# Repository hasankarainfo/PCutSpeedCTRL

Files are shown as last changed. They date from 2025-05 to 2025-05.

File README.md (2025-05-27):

# PCutSpeedCTRL Constant Speed Controller

<ul align="left">
    <li>It provides constant speed operation and remote control of single phase AC motor suitable for operation with 220 vac 50hz.</li>
    <li>When produced with BTA41 triac switching element, it provides usage up to 40 Ampere. In my initial tests I used a 1.2kW AC motor.</li>
    <li>The first version component cost was calculated as $3,075.</li>
    <li>Suitable for use with standard hand milling motors that are easily available on the world market.</li>
    <li>The mentioned milling motors are suitable for use in CNC machines.</li>
    <li>Any CNC controller can be connected directly and in isolation with a standard PWM output.</li>
    <li>This resource contains design and production files for hardware and firmware.</li>
    <li>PC Software used in the development process; KICAD 9 for Hardware, MOUNRIVER 2.1 IDE and C programming language were used for Firmware. OCTAVE was used to create look up tables for some mathematical equations.</li>
    <li> <a href="https://youtu.be/PU_BxYYPQiw ">Test Video Youtube Link</a>  </li>  
</ul>  

<table align="center" width=90%>
<tr>       
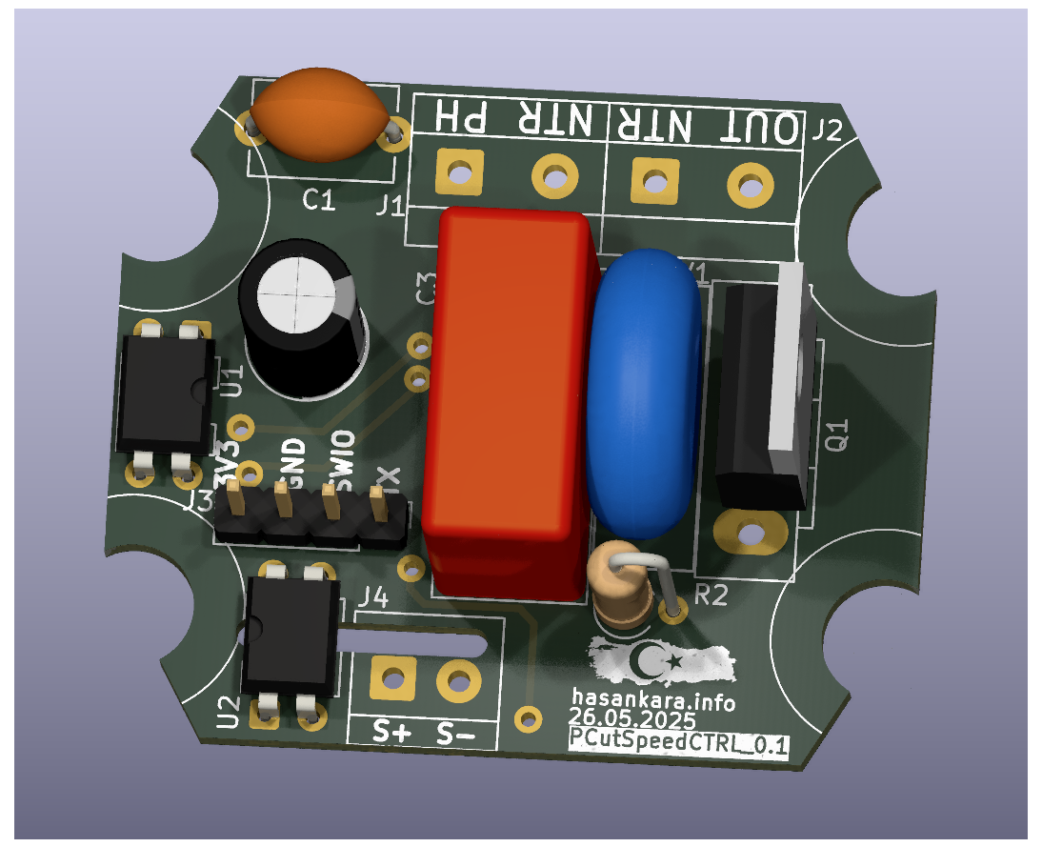
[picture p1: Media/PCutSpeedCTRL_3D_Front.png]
<td align="center"></td>
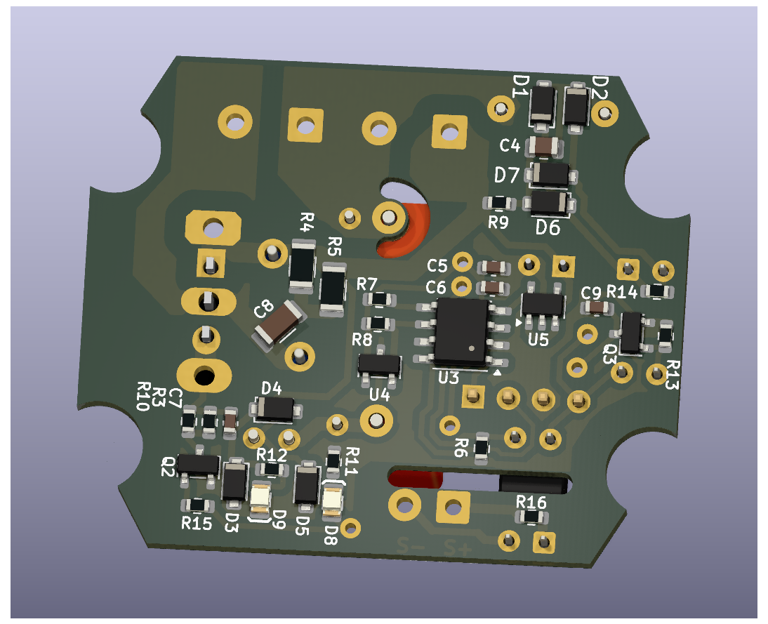
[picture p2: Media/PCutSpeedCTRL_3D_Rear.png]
<td align="center"></td>  
</tr>

<tr>  
<td align="center"> <b>3D Front</b></td>
<td align="center"> <b>3D Rear</b></td>
</tr>
</table>

## HARDWARE Detail:

### Schematic Detail:
<table align="center" width=90%>
    <tr>       
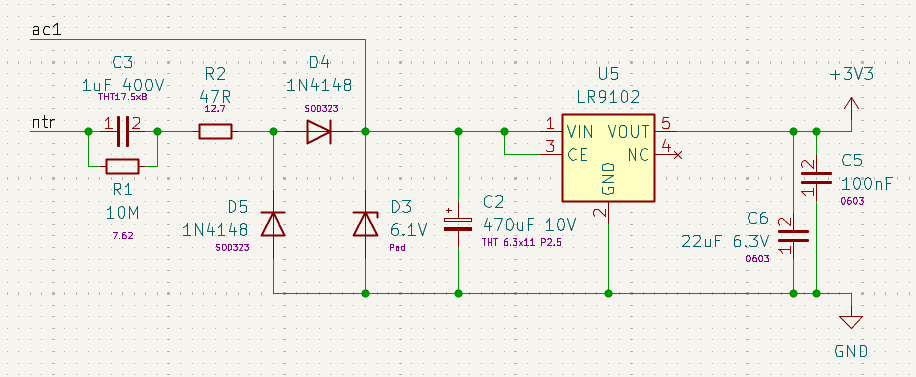
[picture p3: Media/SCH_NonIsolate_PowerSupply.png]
        <td style="width:70%"></td>
        <td>
        Non Isolated Power Supply:
            <ul><i> 
                <li> A cost-effective, non-isolated design was implemented for low voltage supply needs.  </li> 
                <li> This scheme can meet the required 30mA power requirement. This power is mainly used for MCU operation, hall effect sensor operation and TRIAC triggering.</li> 
            </i></ul>
        </td>  
    </tr>
</table>

<table align="center" width=90%>
    <tr>       
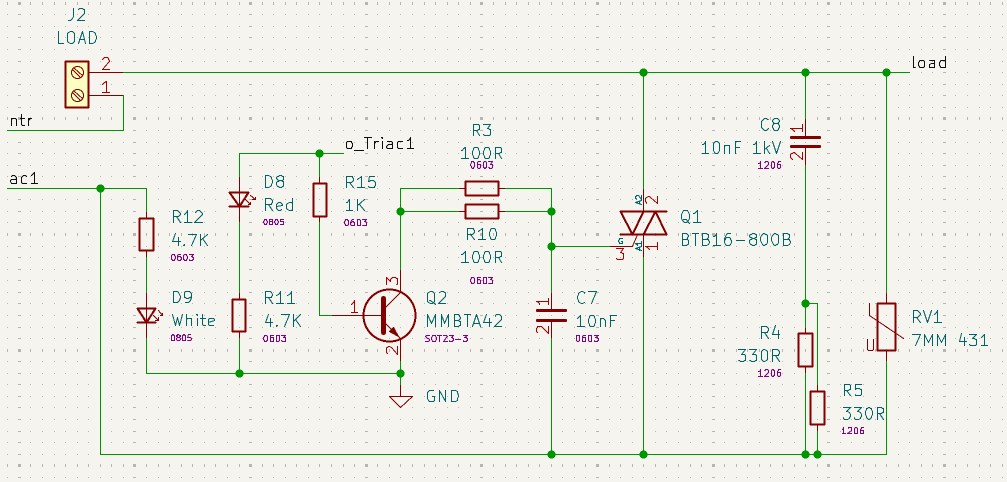
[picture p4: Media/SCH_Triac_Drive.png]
        <td style="width:70%"></td>
        <td> 
        Triac gate drive circuit:
            <ul><i>
            <li>Phase cut topology used.</li> 
            <li> Some snubber components applied.</li> 
            </i></ul>
        </td>  
    </tr>
</table>
<table align="center" width=90%>
    <tr>       
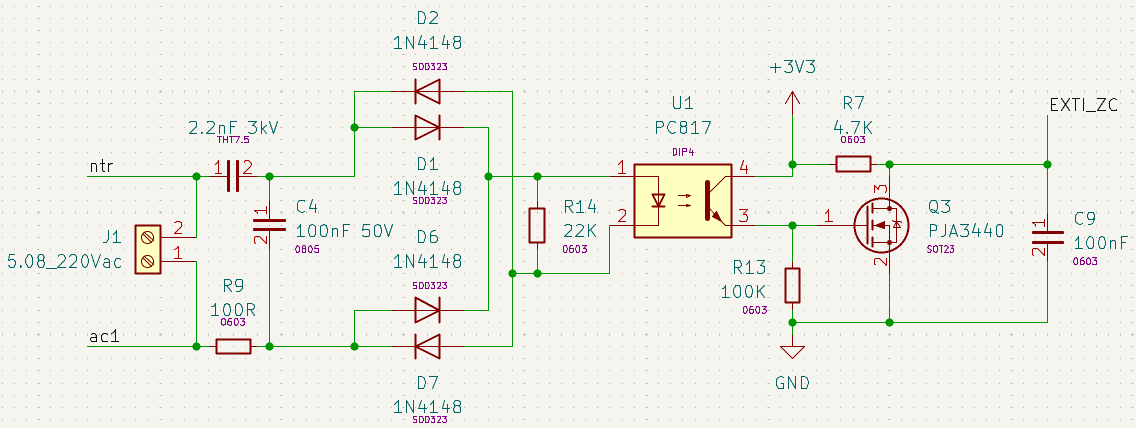
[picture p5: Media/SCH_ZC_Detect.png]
        <td style="width:70%"></td>
        <td> 
        Zero cross detection circuit:
            <ul><i>
            <li>With q3 mosfet, a faster falling edge signal is generated.
            </li> 
            </i></ul>
        </td>  
    </tr>
</table>

<table align="center" width=90%>
    <tr>       
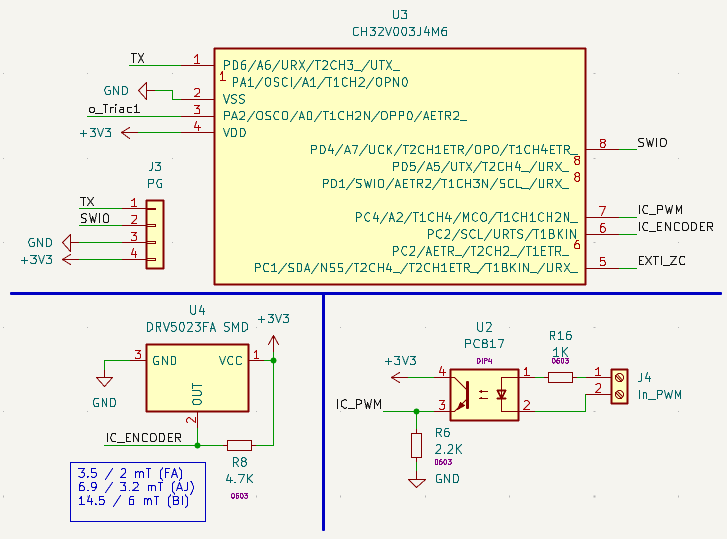
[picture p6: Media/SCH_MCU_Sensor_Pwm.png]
        <td style="width:70%"></td>
        <td> 
        MCU, Hall Sensor and PWM Input Circuit:
            <ul><i>
            <li>It was developed using the ch32v003j4m6 microcontroller from wch company.</li>
            <li> DRV5023 hall sensor was used for spindle speed measurement.</li> 
            </i></ul>
        </td>  
    </tr>
</table>

### Panelize Detail:
<ul align="left">
    <li>We use the Kikit plugin for PCB paneling.</li>
    <li>We can panelize the PCB design by running the panelize_multiple.py file located in the "/HW/Panelize/" file path.</li>
    <li>Phase cut topology used.</li>
    <li>In panelized form, a new kicad project is created automatically.</li>
</ul>  

<table align="center" width=90%>
<tr>       
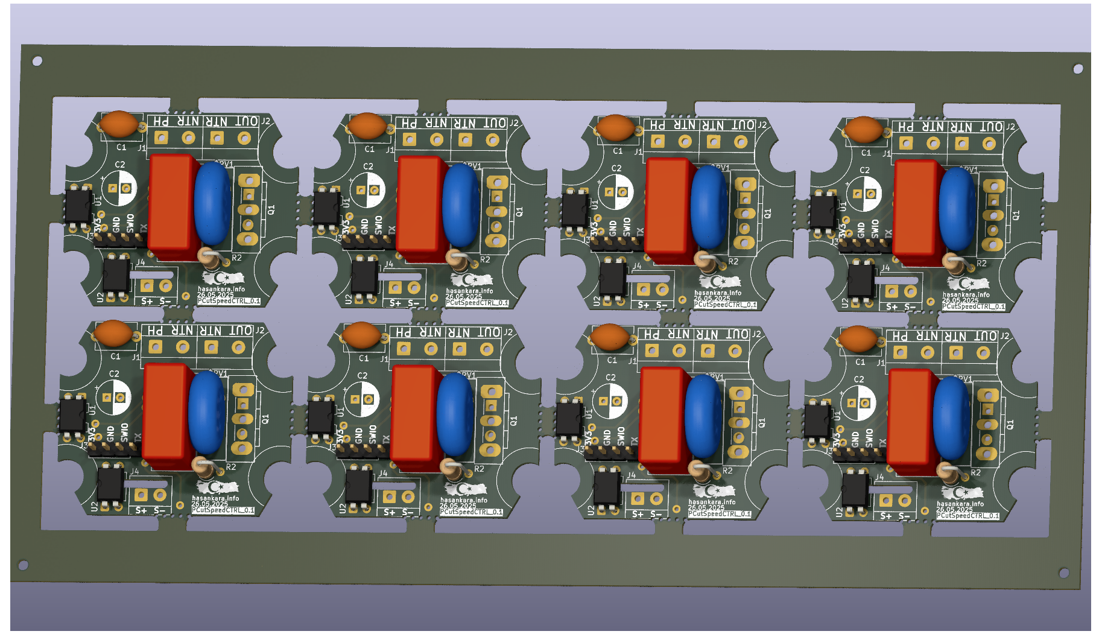
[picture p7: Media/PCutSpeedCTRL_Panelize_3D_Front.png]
<td  style="width:65%"></td>
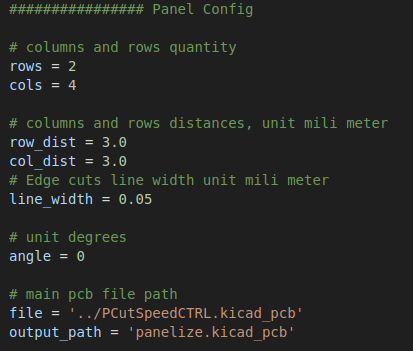
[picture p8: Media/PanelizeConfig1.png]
<td></td>  
</tr>

<tr>  
<td align="center"> <b> Panelize Wiew </b> </td>
<td align="center"> <b> Some Panel Settings in panelize_multiple.py </b></td>
</tr>
</table>

## Mechanic Detail:
<ul align="left"> 
    <li> When the AC motor top cover is opened, 4 screw holes can be seen. 
    </li>
    <li> When the top cover of the spindle motor is first opened, there will be no hole in the middle 
    </li>
    <li> A metric 5 diameter hole should be drilled along the shaft, coinciding with the center.
    </li>
    <li> While designing the PCB, compatibility was ensured by using the Mac Allister manufacturer MSR1200 model AC motor. 
    </li>
</ul>

<table align="center" width=90% >
    <tr>       
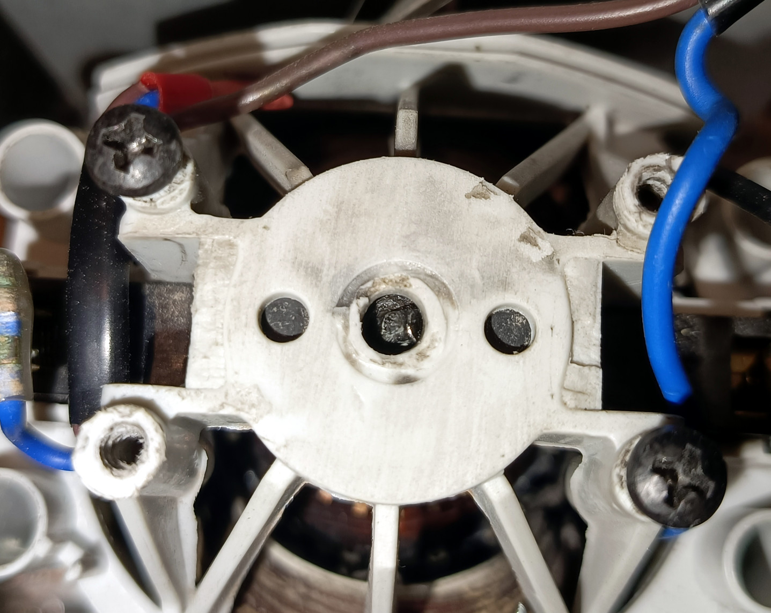
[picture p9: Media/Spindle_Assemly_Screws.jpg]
        <td style="width:70%"></td>
        <td> 
            <ul>
                <li>
                    A 3x3 mm cylindrical neodymium magnet is inserted through this hole and coupled with the shaft.
                </li>
                <li>There should be an angle of approximately ~45° between the magnet cylinder center axis and the shaft axis. 
                </li>
                <li>The shaft and magnet can be attached using super glue.
                </li>
            </ul>
        </td>  
    </tr>
</table>

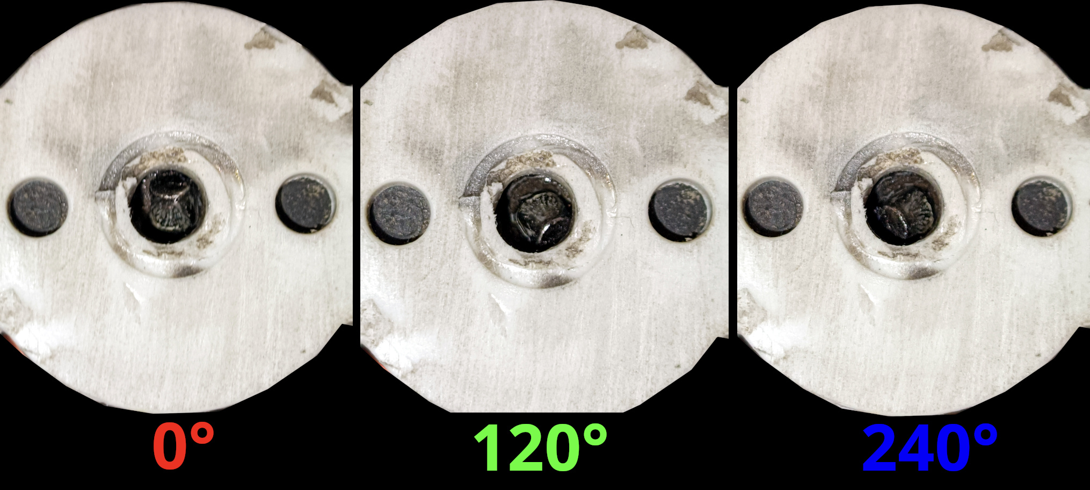
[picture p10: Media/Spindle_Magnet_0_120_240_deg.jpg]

<p align="center"> <b> When the rotor is turned to different angles, it should be confirmed that the magnet rotates together. </b> </p>

<table align="center" width=90% >
    <tr>
        <td>  
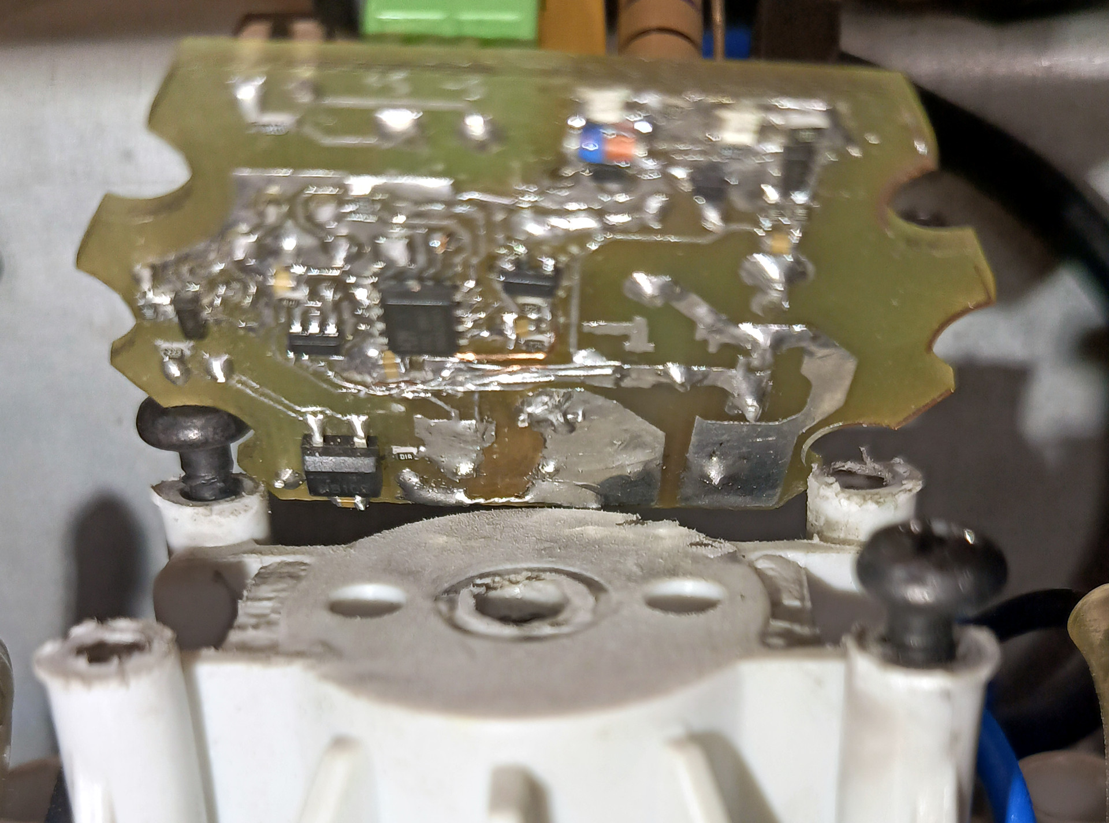
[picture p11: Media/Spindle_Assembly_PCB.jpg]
            
            <p align="center"> <b> Spindle Motor Controller assembly demonstration </b> </p>
        </td>
        <td> 
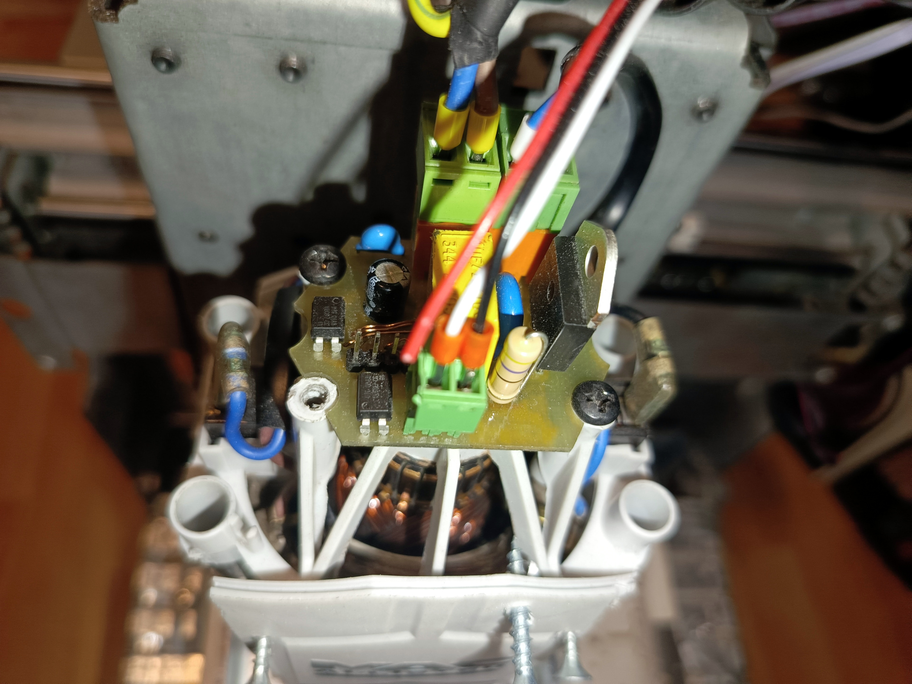
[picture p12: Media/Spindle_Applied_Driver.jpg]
            
            <p align="center"> <b> Spindle Motor Controller Driver Applied </b> </p>
        </td>
    </tr>
</table>

## Firmware Detail:

<ul align="left">
    <li>MOUNRIVER 2.1 IDE and C programming language were used for Firmware.</li>
    <li>The HYB cooperative operating system was used for the MCU resource management organization. </li>
    <li>Since the cooperative real-time operating system we use is very lightweight, it can easily adapt to the Microcontroller despite its weak memory.
    </li>
    <li> With this project, I am also sharing the cooperative operating system that I have been developing over the years as open source.</li>
    <li> I also added some libraries to the firmware that are not actively in use but could enable developments that fit the structure of the project.
    </li>
    <li>NTC temperature sensor data interpretation, ADC reading, moving average filter, some of them. 
    </li>
</ul>  

### About the main routine:
<ul align="left">
    <li>Using 2 different input capture modules, PWM input data was taken with IC1 and the magnetic sensor digital output frequency value was measured with IC2.</li>
    <li>Speed change commands have been smoothed to create a ramp between the PWM data and the target speed information.</li>
    <li>Zero Cross detection was performed using the external interrupt module. Triac triggering and PID routines were run with each ZC detection.</li>
    <li>For linearization of the system, the source signal is assumed to be a sinusoidal signal. The equation used is the integral of the half sine signal.</li>
    <li>For system linearization, PID output information was applied to the linearization function using the look up table interpolation created with the Octave PC application.</li>
    <li>Thus, a more stable closed-loop system was obtained with fixed PID coefficients.
    </li>
    <li>Duty data was evaluated as time data to convert it into TRIAC switch signal.</li>
    <li>In addition to the look up table, a firmware setting option has been added to enable linearization by measurement method.
    </li>
    <li>The firmware can be made to work with different features with a set of predefined settings.</li>
    <li>The mentioned settings can be seen in the image below, as well as in the main.c file.</li>
</ul>  

<td >  
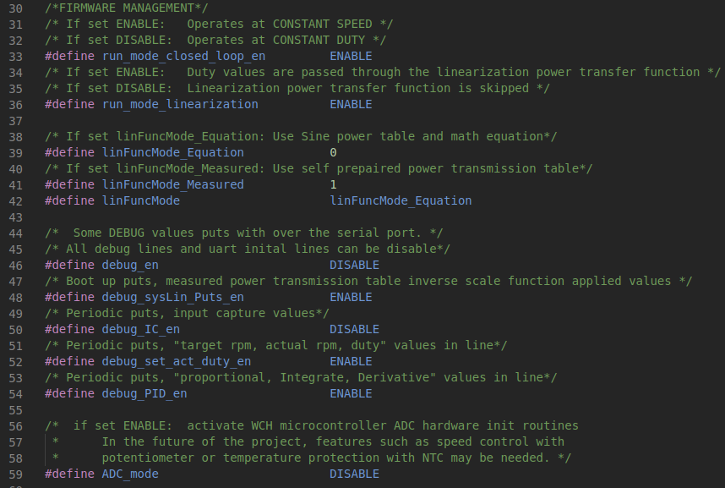
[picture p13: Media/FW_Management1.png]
    
    <p align="center"> <b> Firmware Managment Settings 1 </b> </p>
</td>

<td> 
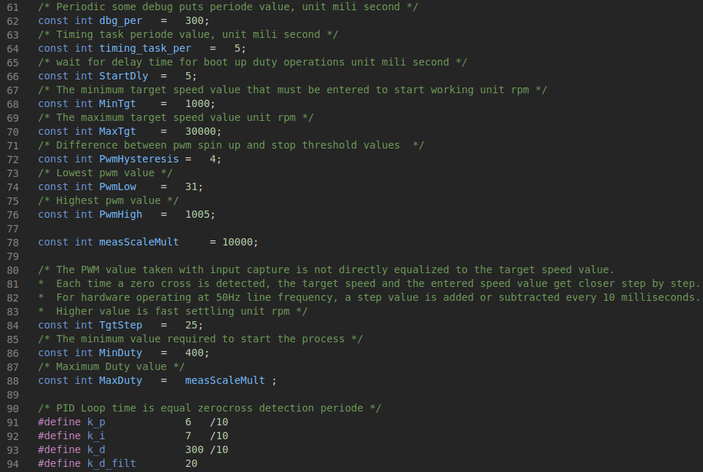
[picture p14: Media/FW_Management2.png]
    
    <p align="center"> <b> Firmware Managment Settings 2 </b> </p>
</td>

### Octave Equations Plot and Print :
<ul align="left">
    <li>The linearization table created with Octave PC software can be examined graphically and can be evaluated by copying and pasting directly into the C code.</li>
    <li>Similarly, the linearization table output from the MCU serial port output at boot up time can be directly copied and pasted into the Octave software and visually inspected. </li>
</ul>  

<table align="center" width=90% >
    <tr>
        <td>  
            
            <p align="center"> <b> Inverse Sine Power Equation Created</b> </p>
        </td>
        <td> 
            
            <p align="center"> <b> Inverse Sine Power from MCU, Equation and Measured </b> </p>
        </td>
    </tr>
</table>

## Some Tests:

<ul align="left">
    <li>As can be watched in the video link shared above, we performed some aluminum sheet and PCB drilling tests.</li>
    <li>When we apply sudden strain and sudden release tests, overshooting values of up to 800 rpm occur.</li>
    <li>The spindle motor we tested has a 30k rpm feature at full power.</li>
    <li>As is known, keeping a constant speed at low rotational speeds can be a very challenging goal.</li>
    <li>Its ability to remain at low overshoot values while at 1k rmp target speed is at a satisfactory level.
    </li>
    <li>We could observe that it does not work so stably unless linearization is applied.</li>
    <li>We made it possible to observe the result by disabling a single predefined setting via the firmware.</li>
</ul>  

<td >  
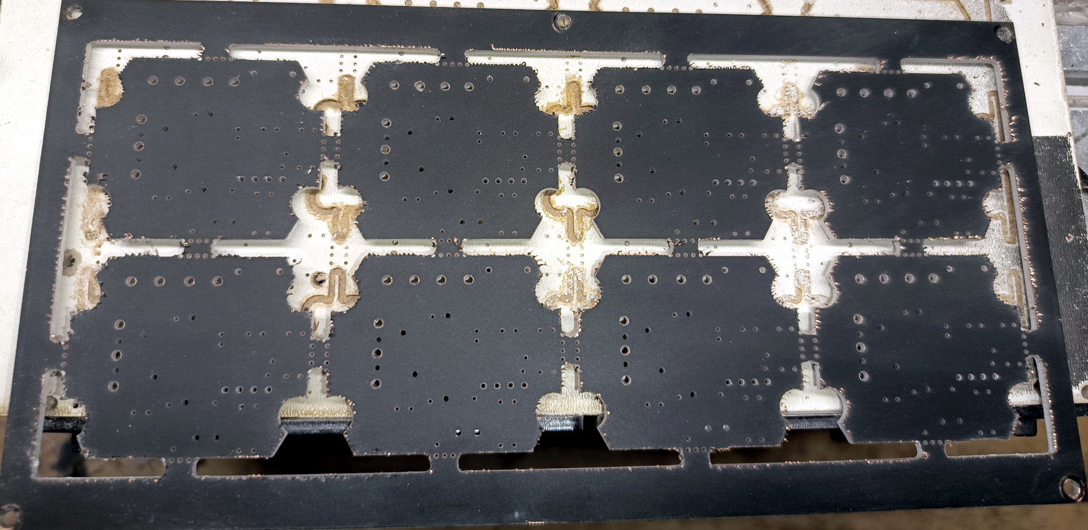
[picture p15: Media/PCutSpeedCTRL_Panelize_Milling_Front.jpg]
    
    <p align="center"> <b> PCB Milling and Edge Cut Test Front </b> </p>
</td>

<td> 
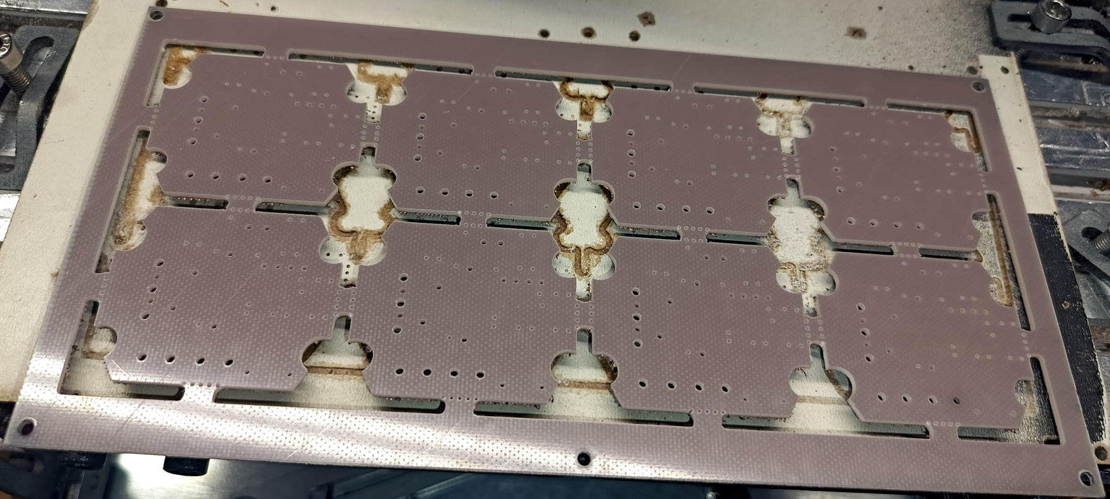
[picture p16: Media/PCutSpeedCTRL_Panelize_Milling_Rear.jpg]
    
    <p align="center"> <b> PCB Milling and Edge Cut Test Rear </b> </p>
</td>

## Production:
<ul align="left">
    <li> Gcode files created for PCB production with DIY techniques can be found in the HW/Panelize/Plot_diy folder.
    </li>
    <li>The bom list, along with supply links and unit prices, can be viewed in the "HW/bom" file path.</li>
    <li>For PCB fabrication files, files in the "HW/Plot" or "HW/Panelize/Plot" file path can be compressed and shared directly with the PCB manufacturer.</li>
</ul>

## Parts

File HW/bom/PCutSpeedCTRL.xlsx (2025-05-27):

 | Sourced | Placed | References | Value | Pad | Part Link | Part Number | Quantity | Price | Q.Price | Total
1 |  |  | C5, C9 | 100nF | 603 | https://ozdisan.com/Product/Detail/476015/CC0603KRX7R9BB104 | CC0603KRX7R9BB104 | 2 | 0.006 | 0.012 | 3.0735
2 |  |  | C1 | 2.2nF 3kV | THT7.5 | https://ozdisan.com/Product/Detail/994897/CK45-B3FD222KYNNA | CK45-B3FD222KYNNA | 1 | 0.35 | 0.35
3 |  |  | C2 | 470uF 10V | THT 6.3x11 P2.5 | https://ozdisan.com/Product/Detail/1046555/PKLH-010V471ME110-T2-5 | PKLH-010V471ME110-T2.5 | 1 | 0.05 | 0.05
4 |  |  | C3 | 1uF 400V | THT17.5x8 | https://www.motorobit.com/1uf-400vdc-15mm-damla-tipi-polyester-kondansator | KOM.KND.03.000133 | 1 | 0.1 | 0.1
5 |  |  | C4 | 100nF 50V | 805 | https://ozdisan.com/Product/Detail/497698/CC0805KRX7R9BB104 | CC0805KRX7R9BB104 | 1 | 0.006 | 0.006
6 |  |  | C6 | 22uF 6.3V | 603 | https://ozdisan.com/Product/Detail/431703/CL10A226MQ8NRNC | CL10A226MQ8NRNC | 1 | 0.038 | 0.038
7 |  |  | C7 | 10nF | 603 | https://ozdisan.com/Product/Detail/9649/CL10B103KB8NNNC | CL10B103KB8NNNC | 1 | 0.006 | 0.006
8 |  |  | C8 | 10nF 1kV | 1206 | https://ozdisan.com/Product/Detail/457676/CC1206KKX7RCBB103 | CC1206KKX7RCBB103 | 1 | 0.05 | 0.05
9 |  |  | R7, R8, R11, R12 | 4.7K | 603 | https://ozdisan.com/Product/Detail/494590/RC0603FR-074K7L | RC0603FR-074K7L | 4 | 0.0018 | 0.0072
10 |  |  | R3, R9, R10 | 100R | 603 | https://ozdisan.com/Product/Detail/341784/0603SAF1000T5E | 0603SAF1000T5E | 3 | 0.0015 | 0.0045
11 |  |  | R4, R5 | 330R | 1206 | https://ozdisan.com/Product/Detail/30259/1206S4F3300T5E | 1206S4F3300T5E | 2 | 0.0039 | 0.0078
12 |  |  | R15, R16 | 1K | 603 | https://ozdisan.com/Product/Detail/341789/0603SAF1001T5E | 0603SAF1001T5E | 2 | 0.0015 | 0.003
13 |  |  | R1 | 10M | 7.62 | Part Link | Part Number | 1 | 0.001 | 0.001
14 |  |  | R2 | 47R | 12.7 | Part Link | Part Number | 1 | 0.001 | 0.001
15 |  |  | R6 | 2.2K | 603 | https://ozdisan.com/Product/Detail/513363/RC0603FR-072K2L | RC0603FR-072K2L | 1 | 0.002 | 0.002
16 |  |  | R13 | 100K | 603 | https://ozdisan.com/Product/Detail/339374/0603SAF1003T5E | 0603SAF1003T5E | 1 | 0.0015 | 0.0015
17 |  |  | R14 | 22K | 603 | https://ozdisan.com/Product/Detail/341794/0603SAF2202T5E | 0603SAF2202T5E | 1 | 0.0015 | 0.0015
18 |  |  | D1, D2, D4, D5, D6, D7 | 1N4148 | SOD323 | https://ozdisan.com/Product/Detail/453557/1N4148WS-HT | 1N4148WS-HT | 6 | 0.014 | 0.084
19 |  |  | D3 | 6.1V | Pad | https://ozdisan.com/Product/Detail/14547/ZMD6-2 | ZMD6.2 | 1 | 0.05 | 0.05
20 |  |  | D8 | Red | 805 | https://ozdisan.com/Product/Detail/490003/HL-PSC-2012H233W-HF4 | HL-PSC-2012H233W-HF4 | 1 | 0.024 | 0.024
21 |  |  | D9 | White | 805 | https://ozdisan.com/Product/Detail/490003/HL-PSC-2012H233W-HF4 | HL-PSC-2012H233W-HF4 | 1 | 0.024 | 0.024
22 |  |  | U1, U2 | PC817 | DIP4 | https://ozdisan.com/Product/Detail/502879/UPC817CG-D04-T | UPC817CG-D04-T | 2 | 0.08 | 0.16
23 |  |  | U3 | CH32V003J4M6 |  | https://aliexpress.com/item/1005005263084570.html | CH32V003J4M6 | 1 | 0.35 | 0.35
24 |  |  | U4 | DRV5023FA SMD |  | https://www.digikey.com/en/products/detail/texas-instruments/DRV5023AJQDBZRQ1/5056028 | 296-49623-1-ND | 1 | 0.8 | 0.8
25 |  |  | U5 | LR9102 |  | https://ozdisan.com/Product/Detail/700883/LR9102G-33-AF5-R | LR9102G-33-AF5-R | 1 | 0.09 | 0.09
26 |  |  | Q1 | BTB16-800B |  | https://www.direnc.net/btb16-800-triac-800v-16a-snubberless-triac-to-220ab |  | 1 | 0.48 | 0.48
27 |  |  | Q2 | MMBTA42 | SOT23-3 | https://ozdisan.com/Product/Detail/348651/MMBTA42R100001 | MMBTA42_R1_00001 | 1 | 0.03 | 0.03
28 |  |  | Q3 | PJA3440 | SOT23 | https://ozdisan.com/Product/Detail/517995/PJA3440R200001 | PJA3440_R2_00001 | 1 | 0.1 | 0.1
29 |  |  | RV1 | 7MM 431 |  | https://ozdisan.com/Product/Detail/339778/TVR07431KSABY | TVR07431KSABY | 1 | 0.05 | 0.05
30 |  |  | J1 | 5.08_220Vac |  | https://ozdisan.com/Product/Detail/1042573/ZB2EDGV-5-08-2P | ZB2EDGV-5.08-2P | 1 | 0.045 | 0.045
31 |  |  | J2 | LOAD |  | https://ozdisan.com/Product/Detail/1042573/ZB2EDGV-5-08-2P | ZB2EDGV-5.08-2P | 1 | 0.045 | 0.045
32 |  |  | J4 | In_PWM |  | https://ozdisan.com/Product/Detail/707708/15EDGVC-3-5-02P-12-00AH | 15EDGVC-3.5-02P-12-00AH | 1 | 0.1 | 0.1

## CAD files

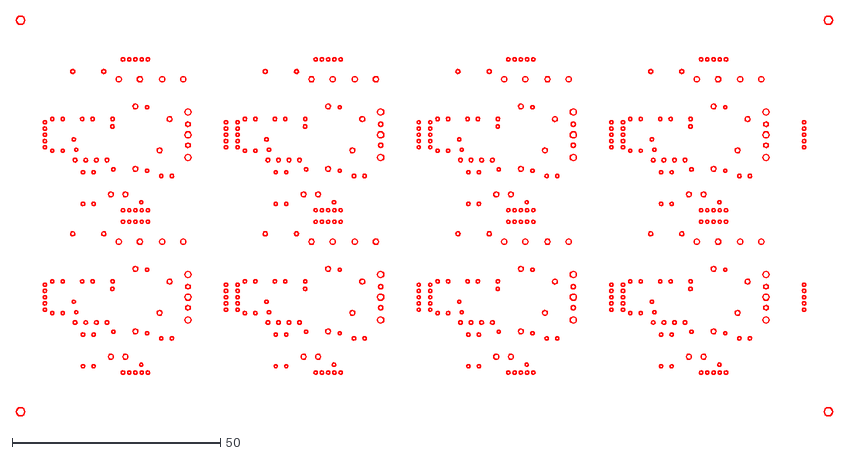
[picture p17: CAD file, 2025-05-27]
HW/Panelize/Plot_diy/panelize.dxf
196.0 x 96.0

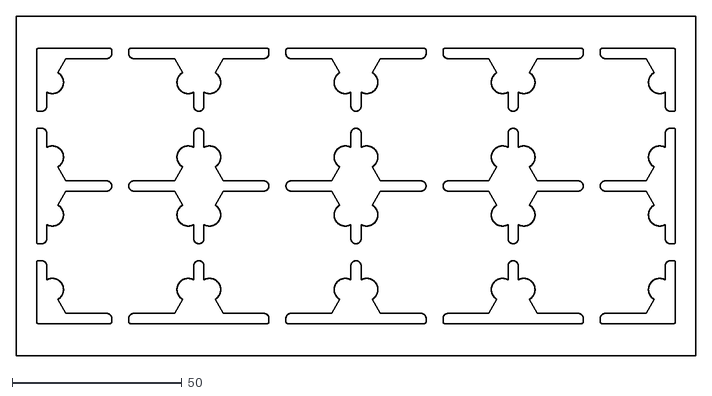
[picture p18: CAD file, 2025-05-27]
HW/Panelize/Plot_diy/panelize-Edge_Cuts.dxf
200.0 x 100.0

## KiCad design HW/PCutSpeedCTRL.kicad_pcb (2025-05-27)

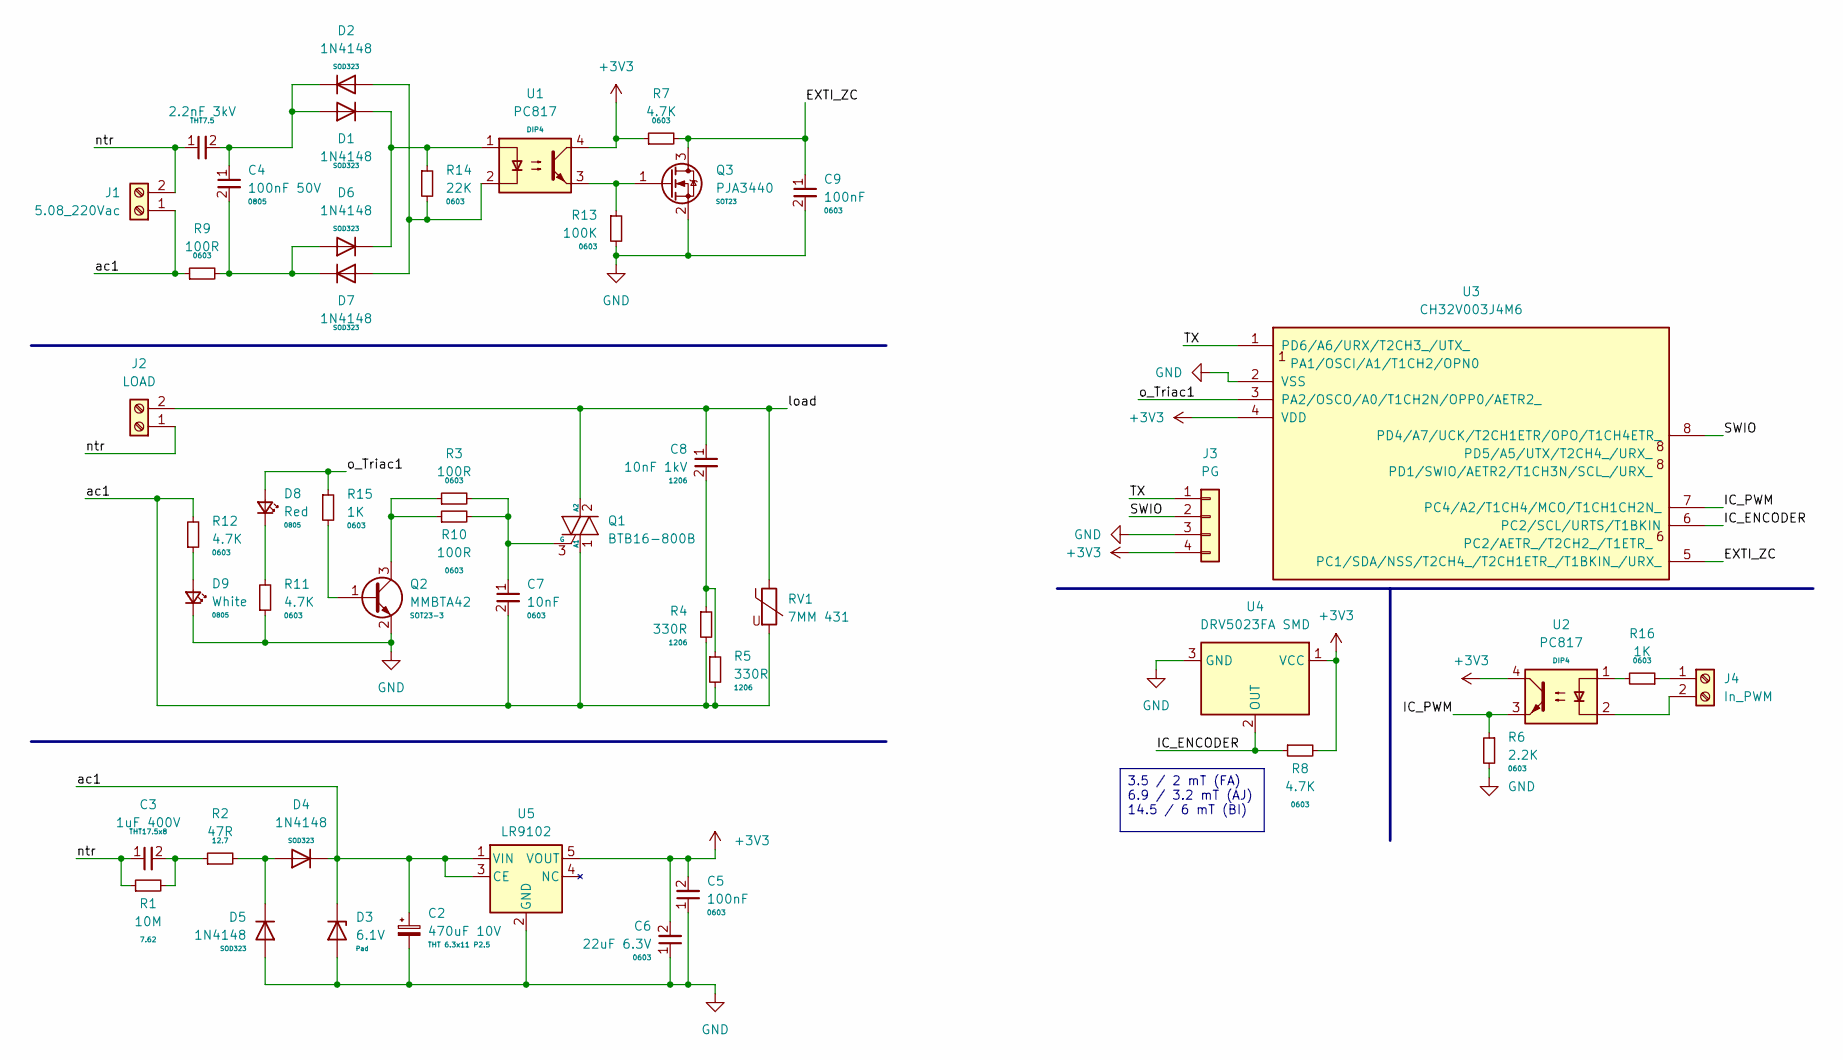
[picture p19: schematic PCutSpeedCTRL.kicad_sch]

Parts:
C1: 2.2nF 3kV; C_Disc_D7.5mm_W5.0mm_P7.50mm; Part Number CK45-B3FD222KYNNA
C2: 470uF 10V; CP_Radial_D6.3mm_H11.0mm_P2.50mm; Part Number PKLH-010V471ME110-T2.5
C3: 1uF 400V; C_Rect_L18.0mm_W8.0mm_P15.00mm_FKS3_FKP3; Part Number KOM.KND.03.000133
C4: 100nF 50V; C_0805_2012Metric_SmallPad; Part Number CC0805KRX7R9BB104
C5, C9: 100nF; C_0603_1608Metric_SlimPad; Part Number CC0603KRX7R9BB104
C6: 22uF 6.3V; C_0603_1608Metric; Part Number CL10A226MQ8NRNC
C7: 10nF; C_0603_1608Metric_SlimPad; Part Number CL10B103KB8NNNC
C8: 10nF 1kV; C_1206_3216Metric_SlimPad; Part Number CC1206KKX7RCBB103
D1, D2, D4, D5, D6, D7: 1N4148; D_SOD-123F-s; Part Number 1N4148WS-HT
D3: 6.1V; D_SOD-123F-s; Part Number ZMD6.2
D8: Red; LED_0805_2012Metric-s; Part Number HL-PSC-2012H233W-HF4
D9: White; LED_0805_2012Metric-s; Part Number HL-PSC-2012H233W-HF4
J1: 5.08_220Vac; TerminalBlock_MetzConnect_Type101_RT01602HBWC_1x02_P5.08mm_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; Part Number ZB2EDGV-5.08-2P
J2: LOAD; TerminalBlock_MetzConnect_Type101_RT01602HBWC_1x02_P5.08mm_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; Part Number ZB2EDGV-5.08-2P
J3: PG; PinHeader_1x04_P2.54mm_Vertical
J4: In_PWM; TerminalBlock_4Ucon_1x02_P3.50mm_Horizontal; Part Number 15EDGVC-3.5-02P-12-00AH
Q1: BTB16-800B; TO-220-3_Vertical_HV_TO247_Applied
Q2: MMBTA42; SOT-23-3-s; Part Number MMBTA42_R1_00001
Q3: PJA3440; SOT-23-3-s; Part Number PJA3440_R2_00001
R1: 10M; R_Axial_DIN0207_L6.3mm_D2.5mm_P15.24mm_Horizontal; Part Link Part Link
R2: 47R; R_Axial_DIN0309_L9.0mm_D3.2mm_P2.54mm_Vertical; Part Link Part Link
R3, R9, R10: 100R; R_0603_1608Metric; Part Number 0603SAF1000T5E
R4, R5: 330R; R_1206_3216Metric_SlimPad; Part Number 1206S4F3300T5E
R6: 2.2K; R_0603_1608Metric; Part Number RC0603FR-072K2L
R7, R8, R11, R12: 4.7K; R_0603_1608Metric; Part Number RC0603FR-074K7L
R13: 100K; R_0603_1608Metric; Part Number 0603SAF1003T5E
R14: 22K; R_0603_1608Metric; Part Number 0603SAF2202T5E
R15, R16: 1K; R_0603_1608Metric; Part Number 0603SAF1001T5E
RV1: 7MM 431; RV_Disc_D15.5mm_W5.4mm_P7.5mm_Spec; Part Number TVR07431KSABY
U1, U2: PC817; DIP-4_W7.62mm; Part Number UPC817CG-D04-T
U3: CH32V003J4M6; SO-8_3.9x4.9mm_P1.27mm; Part Number CH32V003J4M6
U4: DRV5023FA SMD; SOT-23-3-s; Part Number 296-49623-1-ND
U5: LR9102; TSOT-23-5_SlimPad; Part Number LR9102G-33-AF5-R

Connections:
+3V3: C5.2, C6.2, J3.4, R7.1, R8.2, U1.4, U2.4, U3.4 (VDD), U4.1 (VCC), U5.5 (VOUT)
/EXTI_ZC: C9.1, Q3.3 (D), R7.2, U3.5 (PC1/SDA/NSS/T2CH4_/T2CH1ETR_/T1BKIN_/UR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)
/IC_ENCODER: R8.1, U3.6 (PC2/SCL/URTS/T1BKIN), U4.2 (OUT)
/IC_PWM: R6.1, U2.3, U3.7 (PC4/A2/T1CH4/MCO/T1CH1CH2N_)
/SWIO: J3.2, U3.8 (PD4/A7/UCK/T2CH1ETR/OPO/T1CH4ETR_)
/TX: J3.1, U3.1 (PD6/A6/URX/T2CH3_/UTX_)
/ac1: C2.1, C7.2, D3.1 (K), D4.1 (K), J1.1, Q1.1 (A1), R4.2, R5.2, R9.1, R12.2, RV1.2, U5.1 (VIN), U5.3 (CE)
/load: C8.1, J2.2, Q1.2 (A2), RV1.1
/ntr: C1.1, C3.1, J1.2, J2.1, R1.1
/o_Triac1: D8.2 (A), R15.1, U3.3 (PA2/OSCO/A0/T1CH2N/OPP0/AETR2_)
GND: C2.2, C5.1, C6.1, C9.2, D3.2 (A), D5.2 (A), D9.1 (K), J3.3, Q2.2 (E), Q3.2 (S), R6.2, R11.1, R13.2, U3.2 (VSS), U4.3 (GND), U5.2 (GND)
unnamed: C3.2, R1.2, R2.1
unnamed: C8.2, R4.1, R5.1
unnamed: C1.2, C4.1, D1.2 (A), D2.1 (K)
unnamed: D1.1 (K), D6.1 (K), R14.1, U1.1
unnamed: D2.2 (A), D7.2 (A), R14.2, U1.2
unnamed: D4.2 (A), D5.1 (K), R2.2
unnamed: C4.2, D6.2 (A), D7.1 (K), R9.2
unnamed: D8.1 (K), R11.2
unnamed: D9.2 (A), R12.1
unnamed: J4.1, R16.1
unnamed: J4.2, U2.2
unnamed: C7.1, Q1.3 (G), R3.2, R10.2
unnamed: Q2.1 (B), R15.2
unnamed: Q2.3 (C), R3.1, R10.1
unnamed: Q3.1 (G), R13.1, U1.3
unnamed: R16.2, U2.1

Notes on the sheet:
3.5 / 2 mT (FA) 6.9 / 3.2 mT (AJ) 14.5 / 6 mT (BI)

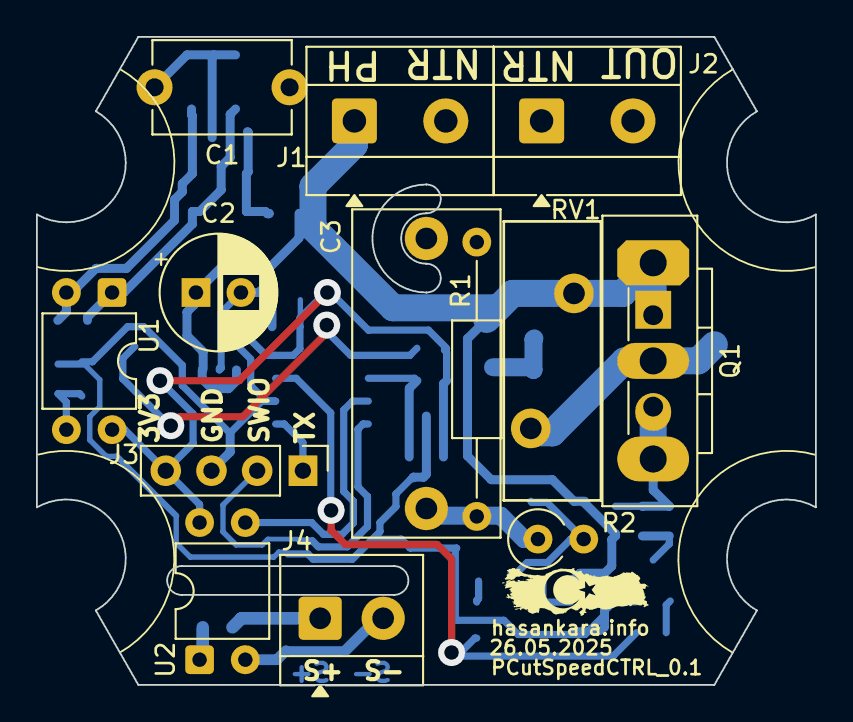
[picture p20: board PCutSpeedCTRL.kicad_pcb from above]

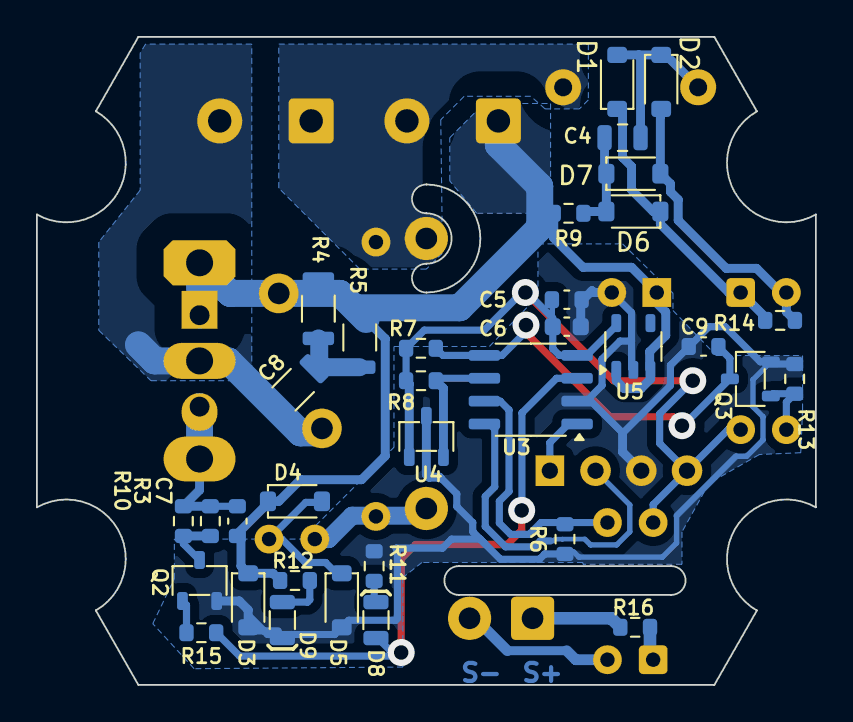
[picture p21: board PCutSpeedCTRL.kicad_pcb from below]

Board: 2 copper layers, 43.3 x 36.0 mm, 47 parts (34 on the bottom side), 27 nets.

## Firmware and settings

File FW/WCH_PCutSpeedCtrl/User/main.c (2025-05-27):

/********************************** (C) COPYRIGHT *******************************
 * File Name          : main.c
 * Author             : hasankarainfo
 * Version            : V_01b
 * Date               : 2025/04/15
 * Description        : WCH_PCutSpeedCTRL main program body. 
 *	It ensures that the motor, suitable for operation with 220 vac 50hz, operates at constant speed.
 *	It was developed using the ch32v003j4m6 microcontroller from wch company.
 *	Some benefits of the firmware;
 *	Suitable for use with standard hand milling motors that are easily available on the world market.
 *	The mentioned milling motors are suitable for use in CNC machines,
 *	Any CNC controller can be connected directly and in isolation with a standard PWM output.
 *********************************************************************************
 * Copyright (c) hasankarainfo
 *******************************************************************************/

#include "init_wch.h"
#include "debug.h"
#include <stdbool.h>
#include "diff_int.h"
#include "NTC_Table.h"

#include "hybos_threads.h"

///\\\-\---\----\------\-------\--------\----------\-----------\-------------
#define DISABLE		0
#define ENABLE 		!DISABLE

///\\\-\---\----\------\-------\--------\----------\-----------\-------------
/*FIRMWARE MANAGEMENT*/
/* If set ENABLE:	Operates at CONSTANT SPEED */
/* If set DISABLE:	Operates at CONSTANT DUTY */
#define run_mode_closed_loop_en			ENABLE
/* If set ENABLE:	Duty values are passed through the linearization power transfer function */
/* If set DISABLE:	Linearization power transfer function is skipped */
#define run_mode_linearization			ENABLE

/* If set linFuncMode_Equation: Use Sine power table and math equation*/
#define linFuncMode_Equation			0
/* If set linFuncMode_Measured: Use self prepaired power transmission table*/
#define linFuncMode_Measured			1
#define linFuncMode						linFuncMode_Equation

/*	Some DEBUG values puts with over the serial port. */
/* All debug lines and uart inital lines can be disable*/
#define debug_en						DISABLE
/* Boot up puts, measured power transmission table inverse scale function applied values */
#define debug_sysLin_Puts_en			ENABLE
/* Periodic puts, input capture values*/
#define debug_IC_en						DISABLE
/* Periodic puts, "target rpm, actual rpm, duty" values in line*/
#define debug_set_act_duty_en			ENABLE
/* Periodic puts, "proportional, Integrate, Derivative" values in line*/
#define debug_PID_en					ENABLE

/*	if set ENABLE:	activate WCH microcontroller ADC hardware init routines
 *		In the future of the project, features such as speed control with 
 *		potentiometer or temperature protection with NTC may be needed. */
#define ADC_mode 						DISABLE

/* Periodic some debug puts periode value, unit mili second */
const int dbg_per	=	300;
/* Timing task periode value, unit mili second */
const int timing_task_per	=	5;
/* wait for delay time for boot up duty operations unit mili second */
const int StartDly	=	5;
/* The minimum target speed value that must be entered to start working unit rpm */
const int MinTgt 	=	1000;
/* The maximum target speed value unit rpm */
const int MaxTgt 	=	30000;
/* Difference between pwm spin up and stop threshold values  */
const int PwmHysteresis =	4; 
/* Lowest pwm value */
const int PwmLow 	=	31;
/* Highest pwm value */
const int PwmHigh 	=	1005;

const int measScaleMult 	= 10000;

/* The PWM value taken with input capture is not directly equalized to the target speed value.
*  Each time a zero cross is detected, the target speed and the entered speed value get closer step by step.
*  For hardware operating at 50Hz line frequency, a step value is added or subtracted every 10 milliseconds.
*  Higher value is fast settling unit rpm */
const int TgtStep 	=	25;
/* The minimum value required to start the process */
const int MinDuty 	=	400; 
/* Maximum Duty value */
const int MaxDuty 	=	measScaleMult ;

/* PID Loop time is equal zerocross detection periode */
#define	k_p				6	/10
#define	k_i				7	/10
#define	k_d				300	/10
#define	k_d_filt		20
///\\\-\---\----\------\-------\--------\----------\-----------\-------------
/*EXTERNS*/
extern hyb_ts *hyb_cooperative_create(void);
extern hyb_ret_te hyb_cooperative_handler(hyb_ts *hyb);
///\\\-\---\----\------\-------\--------\----------\-----------\-------------
const int Periode =	10000; /* zero cross (zc) periode cycle time. unit micro second (us)*/
#define k_rpm				(60*1000)

#if (linFuncMode == linFuncMode_Equation)

/* The table is created With Octave PC Application */
const uint16_t inverseSinePowerAmplitude = 10000;
const uint16_t inverseSinePowerLength = 101;
const uint16_t inverseSinePowerTable[101] = {
   0,  638,  903, 1108, 1282, 1436, 1575, 1705, 1826, 1940,
2048, 2152, 2252, 2348, 2441, 2532, 2620, 2706, 2789, 2871,
2952, 3031, 3108, 3184, 3259, 3333, 3406, 3478, 3550, 3620,
3690, 3759, 3828, 3896, 3963, 4030, 4097, 4163, 4229, 4294,
4359, 4424, 4489, 4553, 4617, 4681, 4745, 4809, 4873, 4936,
5000, 5064, 5127, 5191, 5255, 5319, 5383, 5447, 5511, 5576,
5641, 5706, 5771, 5837, 5903, 5970, 6037, 6104, 6172, 6241,
6310, 6380, 6450, 6522, 6594, 6667, 6741, 6816, 6892, 6969,
7048, 7129, 7211, 7294, 7380, 7468, 7559, 7652, 7748, 7848,
7952, 8060, 8174, 8295, 8425, 8564, 8718, 8892, 9097, 9362,
10000};

#elif (linFuncMode == linFuncMode_Measured)
/*	Attention Please;
	The minimum value of all values in the table must be at index [0]
	The maximum value of all values in the table must be at index [Length-1]

	Duty is increased at equal intervals and the feedback value is recorded.
	When performing this operation, "run_mode_closed_loop_en DISABLE", must be used.
	When performing this operation, "run_mode_linearization DISABLE", must be used.
*/
/*	Duty - Power Table	 */
const uint16_t measTable[] 	= {75,121,202,321,452,555,655,716,755,762,765};
const int measTable_Length 	= (sizeof(measTable)/2);
#endif
///\\\-\---\----\------\-------\--------\----------\-----------\-------------

static long limit(long x, long min, long max) {
	long val = x;
	if (max < min) {
		if (val > min)
			val = min;
		if (val < max)
			val = max;
	} else {
		if (val > max)
			val = max;
		if (val < min)
			val = min;
	}
	return val;
}
static long map(long x, long in_min, long in_max, long out_min, long out_max) {
	long val = (x - in_min) * (out_max - out_min) / (in_max - in_min) + out_min;
	val = limit(val, out_min, out_max);

	return val;
}
///\\\-\---\----\------\-------\--------\----------\-----------\-------------
/*SOME GLOBAL VARIABLES*/

int Summ = 0;
int prevError = 0;
int Portional = 0;
int Deriv = 0;
int Duty = 0;
int error = 0;
int tgt_rpm;
int pwm_in;
int act_rpm;
int act_ms;
int calc_us;

uint8_t	f_cnt1 = 0;
uint8_t	f_cnt2 = 0;

hyb_ts	*hyb_globes, *hyb_zc_detect, *hyb_triac_sgn;
diff_ts d_zc;
///\\\-\---\----\------\-------\--------\----------\-----------\-------------
/*VARIABLES and FUNCTIONS for ADC*/
#if (ADC_mode == ENABLE)

typedef enum {
	arg_throttle,
	arg_periode,
	//arg_min, /**/
	//arg_offset,
	arg_size
} arg_enumeration;
//static uint8_t adc_chs[]={ADC_Channel_2, ADC_Channel_0 , ADC_Channel_3, ADC_Channel_1};
// static uint8_t adc_chs[]={ADC_Channel_2, ADC_Channel_0 };
static uint8_t adc_chs[]={ADC_Channel_6, ADC_Channel_7 };
static uint8_t adc_nbrs = arg_size;

static diff_ts d_adc[arg_size];
long arg[arg_size];
long adc_val[arg_size];
long per_raw;

///\\\-\---\----\------\-------\--------\----------\-----------\-------------
void ADC_Result_Rdy(void) {
	//	temp = NTC_ADC2Temperature(ntc);

	//	arg[arg_periode] = map(diff_peek(&d_adc[arg_periode]) , 25,1010,0 , 12000);
	//	arg[arg_min] = map(diff_peek(&d_adc[arg_min]) , 0,1020, 0 , arg[arg_periode]/2);
	//	arg[arg_throttle] = map(diff_peek(&d_adc[arg_throttle]), 25, 1010, 0, arg[arg_periode]- 500);
	//	arg[arg_throttle] = map(diff_peek(&d_adc[arg_throttle]), 25, 1010, 0, 100);
	//	PWM_SET(arg[arg_throttle]/5);
}
#endif
///\\\-\---\----\------\-------\--------\----------\-----------\-------------


#if (linFuncMode == linFuncMode_Equation)

///\\\-\---\----\------\-------\--------\----------\-----------\-------------
int inverseScaleEquation(int in)
{
	int step =0;
	int y1;
	int tmp = 0;
	int val = in;
	
	step = measScaleMult/2;
	y1 = step;

	while(  1 )
	{
		step/=2;
		//tmp = sinus_power_equation(y1);
		if(val < tmp)
		{
			y1-=step;
		}else if(val > tmp){
			y1+=step;
		} else{
			/* exact found*/
			break;
		}
		if(step<1)
		{
			break;
		}
		
	}
		
	return y1;
}
///\\\-\---\----\------\-------\--------\----------\-----------\-------------
int interpolateTable(int in, const uint16_t *ptr, int len, int Amp)
{
	/* Example; tmp = 250 => ind = 2, valn = 1108, val= 903,  result = 1005 */
	in &=0xefffffff;
	len &=0xefffffff;
	int ind =  in / (len-1);
	if(ind >= (len-1)  ) 
	{
		return ptr[len-1];
	}
	//								step*ind	tmp		step*(ind+1)
	/* result = val + delta_y / (	  200		250		  300)			*/
	int val = ptr[ind];
	int valn = ptr[ind+1];
	//result = val + (valn-val) * (tmp - ind*step )/ step;
	return val + (valn-val) * (in*(len-1) - ind*Amp )/ Amp;
}
#elif (linFuncMode == linFuncMode_Measured)
/*********************************************************************
 * @fn      inverseInterpolateTable
 *
 * @brief   The lookup table obtained with the unit impulse response of the system is processed.
 *			The table is scaled and inverse is applied.
 *			Two points are detected and linear interpolation is applied.
 *
 * @param 	in - entering value
 *			ptr - Table Pointer
 *			len - Table Length
 *			scale - scale factor value
 *
 * @return  Resulting value
 */
int inverseInterpolateTable(int in, const uint16_t *ptr, int len, int scale)
{
	int f_val = 0;
	int l_val = 0;
	int width = 0;
	int val=0, valn=0;
	int j=0;
	int delta_x = 0;
	int delta_y = 0;

	f_val = ptr[0];
	//f_val = 0;
	l_val = ptr[len - 1];
	width = l_val - f_val;

	while(  j < len )
	{
		val = (ptr[j] - f_val)* scale /width ;//1087
		j++;
		valn= (ptr[j] - f_val) * scale /width ;//1753

		/* search index*/
		if(val <= in && in <= valn)
		{
			break;
		}
	}

	/* example => valn = 5000, val = 1000, in = 4000, j = 5  */
	delta_y = (valn-val); // delta_y = 4000
	/* delta_x = ((j+1) -j) * scale/len;	*/
	delta_x = scale / len; // delta_x = 909

	/*
	val 	-> in 		3 step
	in 		-> valn 	1 step
	
	fraction = (delta_x)	* ( (in-val) 	/	delta_y 	)
	fraction = (delta_x) 	* (	(3 step) 	/ 	(4 step) 	)
	fraction = 	 909 		* 		3 		/ 		4 			= 682

	result = j * delta_x + fraction
	result = j * delta_x + (delta_x)* ( (in-val) 	/	delta_y 	)
	result = j * delta_x + (delta_x)* ( (in-val) 	/	(valn-val) 	)
				5	  909		 909		 3000 		/ 	  4000
	result = 5 * 909 + 682 = 5227
	*/

	if(delta_y == 0) return 0;
	//return  j * delta_x +  (in - val) * delta_x  / delta_y; 

	// for more fraction
	return  j * scale / len +  (in - val) * scale / len / delta_y; 
}
///\\\-\---\----\------\-------\--------\----------\-----------\-------------
#endif
///\\\-\---\----\------\-------\--------\----------\-----------\-------------

int sys_linearization(int numerator)
{
	/* system linearisation with the sinus function integral and power equation targeting*/
	/* "https://www.desmos.com/calculator/x6jm10zomc" link available to see the chart*/
	int tmp = numerator;
#if (linFuncMode == linFuncMode_Equation)
	// tmp = map(tmp,MinDuty,measScaleMult, MinDuty, MaxDuty);

	tmp = interpolateTable(tmp, inverseSinePowerTable, inverseSinePowerLength, inverseSinePowerAmplitude);

#elif (linFuncMode == linFuncMode_Measured)
	
	tmp = inverseInterpolateTable(tmp, measTable, measTable_Length, measScaleMult);
#endif

	return tmp;
}
///\\\-\---\----\------\-------\--------\----------\-----------\-------------

void task_zc_detect(hyb_ts *hyb){
	hyb_begin;

	while (1)
	{
		if(hyb_get_sgnparam() == 0)
			hyb_suspend();

		hyb_get_sgnparam() = 0;

		if(tgt_rpm   < MinTgt){
			Duty = 0;
			Summ = 0;
			error = tgt_rpm - act_rpm;
			prevError = error;
			continue;
		}
	
#if (run_mode_closed_loop_en == ENABLE)
		int tmp = 0;
		int k_sens_reaction = limit(act_ms,10,300);
		error = tgt_rpm - act_rpm;

		/* P */
		Portional = error  * k_p ;
		Portional = limit(Portional, -measScaleMult/2, measScaleMult/2 );

		/* I */
		tmp = error  * k_i  / k_sens_reaction;
		Summ += tmp;
		Summ = limit(Summ, 200, measScaleMult);

		/* D */
		tmp = (error - prevError) * k_d / k_sens_reaction;
		//tmp = (error - prevError) * k_d ;
		Deriv = (tmp + Deriv*k_d_filt)/(k_d_filt+1);/* filter apply*/
		Deriv = limit(Deriv, -measScaleMult/2, measScaleMult/2 );
		
		/* TOTAL */
		Duty = Portional + Summ + Deriv ;
		prevError = error;
#else 
		/* tgt_rpm values must be remap for duty*/
		if(tgt_rpm >= MinTgt)
			Duty = map(tgt_rpm, MinTgt, MaxTgt, 0, MaxDuty);
		else Duty = 0;

#endif
	Duty = limit(Duty, 0, measScaleMult );

#if (run_mode_linearization == ENABLE)
		Duty = sys_linearization(Duty);
#endif
		
		calc_us = diff_get(&d_zc);
		if(Duty >= MinDuty )
		{
			int time = Periode - Duty - calc_us;
			hyb_wait(time);
			/* If the zc signal occurs during this time, the currently running cycle is skipped.*/
			if(hyb_get_sgnparam() == 0)
			{
				hyb_notify(hyb_triac_sgn,  0);
			}
			
		}else {
			Duty = 0;
		}
		
	}
	hyb_end;
}
///\\\-\---\----\------\-------\--------\----------\-----------\-------------
void zc_detected(void){
	//if(isZc()!=0)return;
	diff_reset(&d_zc);
	hyb_notify(hyb_zc_detect,  (int*)!0);
}

///\\\-\---\----\------\-------\--------\----------\-----------\-------------
void task_triac_sgn(hyb_ts *hyb){
	hyb_begin;

	while (1)
	{
		hyb_suspend();
		Triac(1);
		hyb_delay(500+Duty/4);
		
		Triac(0);
	}
	hyb_end;
}

///\\\-\---\----\------\-------\--------\----------\-----------\-------------
/* PWM Input*/
void IC1_det(uint16_t ris, uint16_t fal)
{
	static int estimate;
	
	int tmp = fal* (PwmHigh + 5) / ris;
	estimate = (tmp + estimate * 9)/10;

	if(estimate*15/10 > tmp &&
	estimate*5/10 < tmp)
	{
		f_cnt1 = 0;
		pwm_in = tmp;
	}
}
///\\\-\---\----\------\-------\--------\----------\-----------\-------------
/* Speed Measure*/
void IC2_det(uint16_t ris, uint16_t fal)
{
	static int estimate;
	
	int tmp = fal;
	estimate = (tmp + estimate * 9)/10;

	if(estimate*15/10 > tmp &&
	estimate*5/10 < tmp)
	{
		f_cnt2 = 0;
		act_ms = tmp/255;
		act_rpm = ((int)k_rpm*255/fal);
	}
}
///\\\-\---\----\------\-------\--------\----------\-----------\-------------
void ramp_tgt_rpm()
{
	static char before_state ;
	int tmp = pwm_in;

	if(tmp   < (PwmLow - before_state * PwmHysteresis)){
		before_state = 0;
		if(tgt_rpm > TgtStep)	tgt_rpm -= TgtStep;
		else {
			tgt_rpm = 0;
		}
		
		
	}
	else {
		before_state = 1;
		tmp = map(tmp, PwmLow, PwmHigh, MinTgt, MaxTgt);
		if		(tmp > tgt_rpm + TgtStep)	tgt_rpm += TgtStep;
		else if	(tmp + TgtStep < tgt_rpm )	tgt_rpm -= TgtStep;
		else 								tgt_rpm = tmp;
	}
}
///\\\-\---\----\------\-------\--------\----------\-----------\-------------
/* Some values Timeout and Ramp handler Task Callback Function */
void task_timing_handler(hyb_ts *hyb){
	hyb_begin;

#if (debug_en == ENABLE)
	USART_Printf_Init(hyb_globes, 115200);
	debug_printf("init %s %s  \r\n",__DATE__, __TIME__);
	debug_printf("SystemClk:%d\r\n",SystemCoreClock);
	debug_printf( "ChipID:%08x\r\n", DBGMCU_GetCHIPID() );
	
	hyb_thread_create(hyb_globes, &task_debug,0,1);
#endif
#if (ADC_mode == ENABLE)
	for (int i = 0; i < adc_nbrs; i++) {
		diff_init_def(&d_adc[i], &adc_val[i]);
		diff_en_rev_tresh(&d_adc[i], 40);
	}

	/*ADC INIT*/
	ADC_HW_Init(&ADC_Result_Rdy , adc_chs, adc_nbrs, adc_val);
#endif
	/* Init Triac Out */
	Init_TriacOut();
	/* Init IC1 for PWM Input*/
	Input_Capture_Init(0xffff, 48-1, &IC1_det);
	/* Init IC2 for Speed Measure*/
	Input_Capture_Init2(0xffff, 192-1, &IC2_det);

	diff_init_def(&d_zc, &sys_tick_us);

	/* Init External Interrupt for Zero Cross Detection*/
	EXTI_app_Init( &zc_detected );

	hyb_delay(StartDly*1000);

	hyb_zc_detect = hyb_thread_create(hyb_globes, &task_zc_detect, 0, 5);
	hyb_triac_sgn = hyb_thread_create(hyb_globes, &task_triac_sgn, 0, 4);
	 while (1){
		hyb_delay(timing_task_per*1000);
		/* IC1 Command PWM Input*/
		int tmp = f_cnt1 * timing_task_per;
		if(tmp > 300)
		{
			if(isPwm()){

				pwm_in = MaxTgt;
			}else{
				pwm_in = 0;
				Summ = 0;
				prevError = 0;
				Duty = 0;
			}
			
		}else{
			f_cnt1 ++;
		}
		ramp_tgt_rpm();

		/* IC2 Speed Measure*/
		tmp = f_cnt2 * timing_task_per;
		if(tmp > 300)
		{
			act_ms = 300;
			act_rpm = k_rpm/act_ms;
			
		}else{
			if(tmp > act_ms)
			{
				act_ms = tmp;
				act_rpm = k_rpm/act_ms;
			}
			f_cnt2 ++;
		}
	 }
	hyb_end;
}
///\\\-\---\----\------\-------\--------\----------\-----------\-------------

/* Debug Task Callback Function*/
#if (debug_en == ENABLE)
void task_debug(hyb_ts *hyb){
	hyb_begin;
static int i=0, j=0 , step=0;

#if(debug_sysLin_Puts_en == ENABLE)
	step = 100;
	debug_printf("\ninverseSinePowerTable = ([");
	hyb_delay(25000);
	for(i=0 ; i<= measScaleMult ; i+=j)
	{
		debug_printf("...\n");
		for ( j = 0 ;j < step * 10; j += step){
			debug_printf("%04d" , sys_linearization(i+j));
			
			if((i+j) > measScaleMult)break;
			debug_printf(", ");
		}
		hyb_delay(40000);
	}
	debug_printf("]); \n");
#endif

	while (1){
		hyb_delay(dbg_per*1000);
		debug_printf("\n");
#if(debug_IC_en == ENABLE)
		
		debug_printf("R1_F1 %04d_%04d\n" ,  (int)IC_rising,  (int)IC_falling);
		debug_printf("R2_F2 %04d_%04d\n", (int)IC_rising2,  (int)IC_falling2);
#endif
#if(debug_set_act_duty_en == ENABLE)
		debug_printf("Set_ActRpm_Duty %04d_%04d_%04d\n" ,  tgt_rpm,  act_rpm, Duty);
		debug_printf("calc_us %04d\n" ,  calc_us);
#endif
#if(debug_PID_en == ENABLE)
		debug_printf("P_I_D %04d_%04d_%04d\n" , Portional,  (int)Summ, (int)Deriv);
#endif
	 }
	hyb_end;
}
#endif
///\\\-\---\----\------\-------\--------\----------\-----------\-------------
/***************************************************************************/
/********************************	MAIN	********************************/
/***************************************************************************/
int main(void) 
{
	Init_CPU();
	Delay_Init();
	hyb_init_port();
	hyb_globes = hyb_cooperative_create();

	hyb_thread_create(hyb_globes, &task_timing_handler,0,4);
	hyb_cooperative_handler(hyb_globes);
}

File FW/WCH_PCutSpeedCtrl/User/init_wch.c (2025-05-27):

/********************************** (C) COPYRIGHT *******************************
 * File Name          : init_wch.c
 * Author             : hasankarainfo
 * Version            : V_01b
 * Date               : 2025/04/15
 * Description        : init hardware for WCH_PCutSpeedCTRL projects.
*********************************************************************************
* Copyright (c) hasankarainfo
*******************************************************************************/

#include "init_wch.h"

/* Global define */
typedef enum {CMD_OK = 0, CMD_ERR = ~CMD_OK} CmdStatus;


static void (*_IC1_cb)(uint16_t ris, uint16_t fal  );
static void (*_IC2_cb)(uint16_t ris, uint16_t fal  );
static void (*_exti_cb)(void );

///\\\-\---\----\------\-------\--------\----------\-----------\-------------

void Init_CPU(void)
{
	NVIC_PriorityGroupConfig(select_NVIC_PriorityGroup);
	SystemCoreClockUpdate();
}

///\\\-\---\----\------\-------\--------\----------\-----------\-------------

void Init_TriacOut(void)
{
	/*Output Drive Triac*/
    RCC_APB2PeriphClockCmd(RCC_APB2Periph_GPIOA , ENABLE);

	GPIO_InitTypeDef GPIO_InitStructure = { 0 };
	GPIO_InitStructure.GPIO_Mode = GPIO_Mode_Out_PP;
	GPIO_InitStructure.GPIO_Speed = GPIO_Speed_30MHz;
	GPIO_InitStructure.GPIO_Pin = _pin_triac;
	GPIO_Init( _port_triac, &GPIO_InitStructure);
    Triac(0);
}
///\\\-\---\----\------\-------\--------\----------\-----------\-------------
void Input_Capture_Init(u16 arr, u16 psc, void (*cb)(uint16_t ris, uint16_t fal  ))
{
    _IC1_cb = cb;
    GPIO_InitTypeDef        GPIO_InitStructure = {0};
    TIM_ICInitTypeDef       TIM_ICInitStructure = {0};
    TIM_TimeBaseInitTypeDef TIM_TimeBaseInitStructure = {0};
    NVIC_InitTypeDef        NVIC_InitStructure = {0};

    GPIO_InitStructure.GPIO_Mode = GPIO_Mode_IN_FLOATING;
    GPIO_InitStructure.GPIO_Speed = GPIO_Speed_30MHz;

#if (SelectMCU  == CH32V003F) // TSSOP20
    RCC_APB2PeriphClockCmd(RCC_APB2Periph_GPIOC | RCC_APB2Periph_TIM1, ENABLE);
    GPIO_InitStructure.GPIO_Pin = GPIO_Pin_4;
    GPIO_Init(GPIOC, &GPIO_InitStructure);
    TIM_ICInitStructure.TIM_Channel = TIM_Channel_1;
    TIM_ITConfig(TIM1, TIM_IT_CC1 | TIM_IT_CC2  , ENABLE);
    TIM_SelectInputTrigger(TIM1, TIM_TS_TI1FP1);

#elif (SelectMCU  == CH32V003J) // SO8
    RCC_APB2PeriphClockCmd(RCC_APB2Periph_GPIOC | RCC_APB2Periph_TIM1, ENABLE);

    RCC_APB2PeriphClockCmd( RCC_APB2Periph_AFIO , ENABLE );
    

    GPIO_InitStructure.GPIO_Pin = GPIO_Pin_4;
    GPIO_Init(GPIOC, &GPIO_InitStructure);
    GPIO_PinRemapConfig(GPIO_FullRemap_TIM1, ENABLE);

    TIM_ICInitStructure.TIM_Channel = TIM_Channel_1;
    TIM_ITConfig(TIM1, TIM_IT_CC1 | TIM_IT_CC2  , ENABLE);
    TIM_SelectInputTrigger(TIM1, TIM_TS_TI1FP1);
#endif
    TIM_TimeBaseInitStructure.TIM_Period = arr;
    TIM_TimeBaseInitStructure.TIM_Prescaler = psc;
    TIM_TimeBaseInitStructure.TIM_ClockDivision = TIM_CKD_DIV1;
    TIM_TimeBaseInitStructure.TIM_CounterMode = TIM_CounterMode_Up;
    TIM_TimeBaseInitStructure.TIM_RepetitionCounter = 0x00;
    TIM_TimeBaseInit(TIM1, &TIM_TimeBaseInitStructure);

    TIM_ICInitStructure.TIM_ICPrescaler = TIM_ICPSC_DIV4;// default 1
    TIM_ICInitStructure.TIM_ICFilter = 0x03;// default 0
    TIM_ICInitStructure.TIM_ICPolarity = TIM_ICPolarity_Rising;// default rising
    TIM_ICInitStructure.TIM_ICSelection = TIM_ICSelection_DirectTI;// default direct ti
    TIM_PWMIConfig(TIM1, &TIM_ICInitStructure);

    NVIC_InitStructure.NVIC_IRQChannel = TIM1_CC_IRQn;
    NVIC_InitStructure.NVIC_IRQChannelPreemptionPriority = select_NVIC_PriorityGroup;
    NVIC_InitStructure.NVIC_IRQChannelSubPriority = 2;
    NVIC_InitStructure.NVIC_IRQChannelCmd = ENABLE;
    NVIC_Init(&NVIC_InitStructure);

    TIM_SelectSlaveMode(TIM1, TIM_SlaveMode_Reset);
    TIM_SelectMasterSlaveMode(TIM1, TIM_MasterSlaveMode_Enable);

    TIM_Cmd(TIM1, ENABLE);
}
///\\\-\---\----\------\-------\--------\----------\-----------\-------------
void TIM1_CC_IRQHandler(void) __attribute__((interrupt("WCH-Interrupt-fast")));
void TIM1_CC_IRQHandler(void)
{
    static uint16_t ris, fal;
    if( TIM_GetITStatus( TIM1, TIM_IT_CC1 ) != RESET )
    {
        ris = TIM_GetCapture1( TIM1 );
    }

    if( TIM_GetITStatus( TIM1, TIM_IT_CC2 ) != RESET )
    {
        fal = TIM_GetCapture2( TIM1 );
        if(_IC1_cb) _IC1_cb(ris, fal);
    }

    TIM_ClearITPendingBit( TIM1, TIM_IT_CC1 | TIM_IT_CC2 );
}
///\\\-\---\----\------\-------\--------\----------\-----------\-------------
void Input_Capture_Init2(u16 arr, u16 psc, void (*cb)(uint16_t ris, uint16_t fal  ))
{
    _IC2_cb = cb;
    GPIO_InitTypeDef        GPIO_InitStructure = {0};
    TIM_ICInitTypeDef       TIM_ICInitStructure = {0};
    TIM_TimeBaseInitTypeDef TIM_TimeBaseInitStructure = {0};
    NVIC_InitTypeDef        NVIC_InitStructure = {0};

#if (SelectMCU  == CH32V003F) // TSSOP20
    RCC_APB2PeriphClockCmd( RCC_APB2Periph_AFIO | RCC_APB2Periph_GPIOC, ENABLE );
    RCC_APB1PeriphClockCmd( RCC_APB1Periph_TIM2 | RCC_APB1Periph_PWR, ENABLE );
    GPIO_InitStructure.GPIO_Mode = GPIO_Mode_IN_FLOATING;
    GPIO_InitStructure.GPIO_Speed = GPIO_Speed_30MHz;

    GPIO_InitStructure.GPIO_Pin = GPIO_Pin_5;
    GPIO_Init(GPIOC, &GPIO_InitStructure);
    GPIO_ResetBits(GPIOC, GPIO_Pin_1);
    GPIO_PinRemapConfig(GPIO_PartialRemap1_TIM2, ENABLE);

    TIM_ITConfig(TIM2, TIM_IT_CC1 | TIM_IT_CC2  , ENABLE);
    TIM_ICInitStructure.TIM_Channel = TIM_Channel_1;
    TIM_SelectInputTrigger(TIM2, TIM_TS_TI1FP1);

#elif (SelectMCU  == CH32V003J) // SO8

    RCC_APB2PeriphClockCmd( RCC_APB2Periph_AFIO | RCC_APB2Periph_GPIOC, ENABLE );
    RCC_APB1PeriphClockCmd( RCC_APB1Periph_TIM2 | RCC_APB1Periph_PWR, ENABLE );
    GPIO_InitStructure.GPIO_Mode = GPIO_Mode_IN_FLOATING;
    GPIO_InitStructure.GPIO_Speed = GPIO_Speed_30MHz;

    GPIO_InitStructure.GPIO_Pin = GPIO_Pin_2;
    GPIO_Init(GPIOC, &GPIO_InitStructure);
    GPIO_ResetBits(GPIOC, GPIO_Pin_2);
    GPIO_PinRemapConfig(GPIO_PartialRemap1_TIM2, ENABLE);

    TIM_ITConfig(TIM2, TIM_IT_CC1 | TIM_IT_CC2 , ENABLE);
    TIM_ICInitStructure.TIM_Channel = TIM_Channel_2;
    TIM_SelectInputTrigger(TIM2, TIM_TS_TI2FP2);
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
